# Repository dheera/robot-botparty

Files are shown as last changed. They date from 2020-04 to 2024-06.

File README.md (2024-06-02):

# BotParty

A mini telepresence robot. At about $130 total for all parts (including the pictured used Pixel 1 phone), the goal of this robot is to be as inexpensive as possible for a complete telepresence solution.

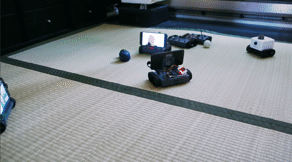
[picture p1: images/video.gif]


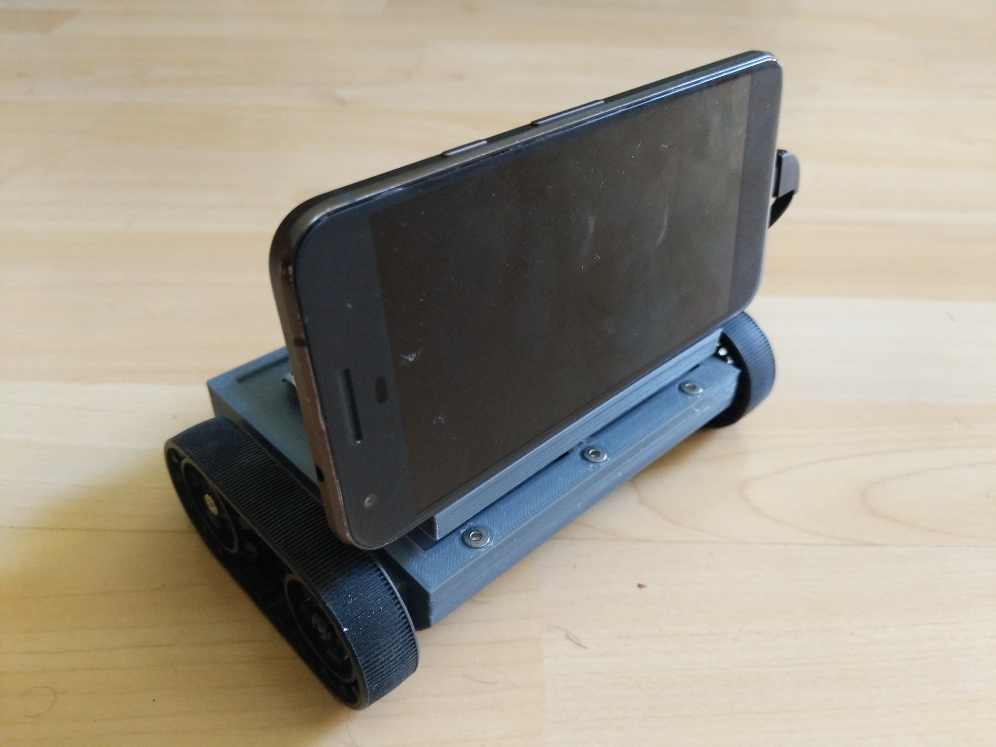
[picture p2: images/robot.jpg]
robot


Completed robot.

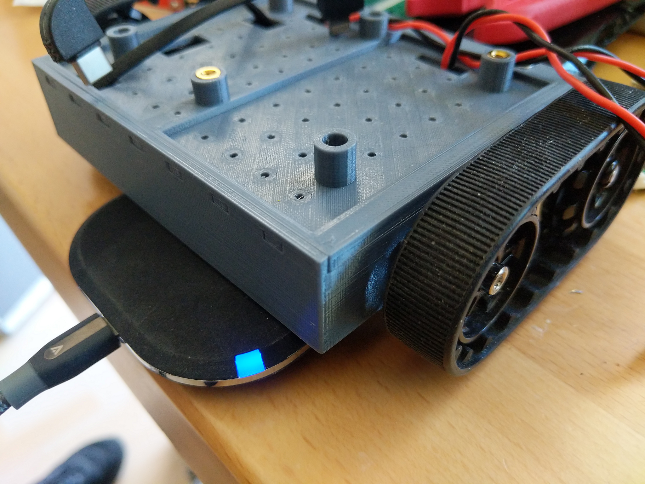
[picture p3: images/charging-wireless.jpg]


If you buy a 5V2A Qi charging sticker, you can charge the robot wirelessly just by driving on top of a wireless charger. Simple and no docking alignment fuss!

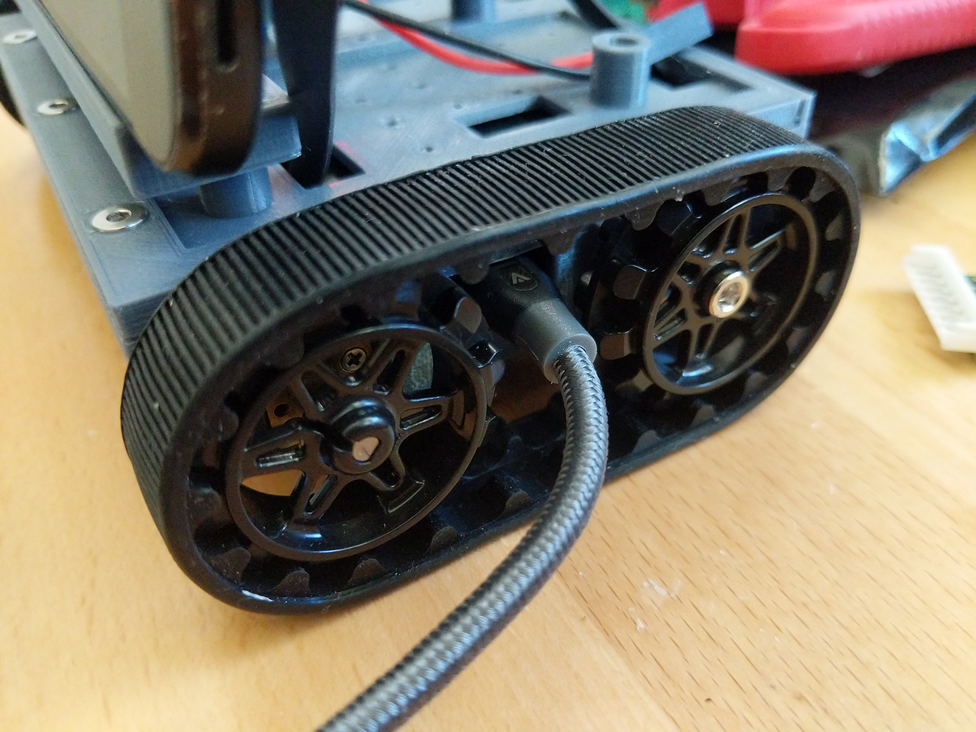
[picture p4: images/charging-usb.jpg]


You can use Anker Powerline micro-USB cables to charge the robot without taking it apart. *Not all micro-USB cables* will clear the outer edge of the sprocket.

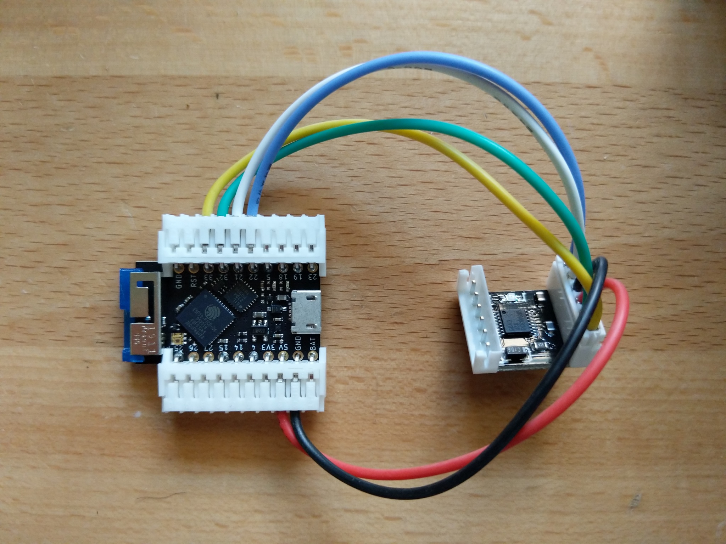
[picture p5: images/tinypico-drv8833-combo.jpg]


The motors are driven by a DRV8833 and a TinyPICO ESP32 microcontroller. The phone talks to the ESP32 over BLE. The ESP32 is super feature packed and also has Wi-Fi, capacitive touch sensing, I2C, SPI, UART, ADC, DAC, and lots of other features so you can build off this design and add whatever sensors and actuators you please. Build a security robot, a robot that roams around sensing VOC gas levels, and more!

## Assembly

### 3D printed parts

See .stl files in design/. I recommend printing in PETG. PLA sucks.

### Mechanical parts

* [M3 short heat-set inserts](https://www.mcmaster.com/94180a331), M3, OD=5.6mm, L=3.8mm -- [Possible alternative](https://www.ebay.com/sch/i.html?_from=R40&_trksid=m570.l1313&_nkw=initeq+m3+long&_sacat=0)
* [M3 long heat-set inserts](https://www.mcmaster.com/94180a333), M3, OD=5.6mm, L=6.4mm -- [Possible alternative](https://www.ebay.com/sch/i.html?_from=R40&_trksid=m570.l1313&_nkw=initeq+m3+short&_sacat=0)
* [Pololu 22T track set](https://www.pololu.com/product/3030)
* [M3 L=5mm countersunk screws](https://www.mcmaster.com/92125a125)
* [M3 L=5mm socket head screws](https://www.mcmaster.com/91292A110)

### Electronics
* [Used Google Pixel 1](https://www.ebay.com/sch/i.html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) -- You can get them used or "refurbished" for under $65. The charging cord on the portable charger below just barely fits so if you buy any bigger phone than the Pixel 1, you may need an extension on the charging cable. I do **not** recommend using an iPhone as Apple is consistently behind the times in terms of in-browser WebRTC support and doesn't even have bluetooth support from the browser. If you use an iPhone you will have to write an iOS native app from scratch.
* 2 x [Micro metal gearmotors](https://www.pololu.com/category/60/micro-metal-gearmotors) -- If you buy from Pololu, HPCB or HP 75:1 is proboblay the best for this use case but you can go up or down to 30:1 to 150:1 depending on your needs. Get single shaft if you don't plan on even putting encoders in, get dual-shaft if you think you might want encoders later. Get MP instead of HP/HPCB if you want a cheaper motor. Or search eBay/AliExpress for MUCH cheaper alternatives although many suppliers don't provide specs on current and stall torque making it hard to choose. There are also sometimes people on eBay reselling authentic used Pololu motors at cheaper prices.
* Portable charger: [YPLANG 9000mAh](https://www.amazon.com/Powerbank-9000mAh-Portable-Charger-External/dp/B07JMTSPC3) or [BeeFix 9000mAh](https://www.amazon.com/Portable-Charger-9000mAh-External-Battery/dp/B07SNV2B42/) or [Elephant Story 9000mAh](http://www.elephantstory.net/product/ds01/) -- They are the same charger under 2 different brand names). Make sure you get the version with 1 USB-C out + 1 lightning+microUSB combination out, and not their older version with 1 microUSB + 1 lightning. The chassis and 3D printed parts are designed to match this charger, which allows charging+discharging at the same time, and has two charging ports, one of which can be used for a Qi charger sticker.
* [2A Qi fast charging receiver USB-C](https://www.aliexpress.com/item/4000239832349.html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,searchweb201602_,searchweb201603_) if you want wireless charging where the robot can just drive up onto a charger (optional)
* 1 x DRV8833 carrier [No-name cheap 5 for $8 carrier](https://www.amazon.com/KOOBOOK-DRV8833-Module-Bridge-Controller/dp/B07S4FVY9M/) or [Pololu 1 for $4.95 DRV8833 carrier](https://www.pololu.com/product/2130) or any other DRV8833 carrier
* [TinyPICO](https://www.adafruit.com/product/4335) or other ESP32 board of your choice
* [24 AWG wire](https://www.amazon.com/gp/product/B07G2BWBX8/)
* [1x2 Dupont connector housing](https://www.pololu.com/product/1901) and [crimps](https://www.pololu.com/product/1930) or just get a [kit like this](https://www.amazon.com/gp/product/B078RRPRQZ/). [This crimper](https://www.amazon.com/Crimping-0-08-1-0-18-28AWG-Ratcheting-Connector/dp/B01N1RFZZ4/) has worked well for me for Dupont crimps.
* [JST-EH](https://www.digikey.com/catalog/en/partgroup/eh-series/) connectors for ESP32 board and ESP-DRV8833 connection (or use whatever you prefer). [This crimper](https://www.amazon.com/Engineers-Precision-Crimping-Pliers-Pa-09/dp/B002AVVO7K/) has worked well for me for JST-EH.

## Code

**esp32/** contains firmware for a TinyPICO. (a) Follow TinyPICO's instructions to enable the Arduino IDE (b) install the analogWrite library for ESP32 and then (c) compile it with Arduino. You can then visit the [ESP32 web terminal](https://dheera.github.io/esp32terminal/) to test connectivity. Steps to test:

- Use desktop Chrome on a laptop that has Bluetooth, or Chrome on Android also works. Chrome on iOS will not work.
- Go to chrome://flags/#enable-experimental-web-platform-features and enable.
- Go to the ESP32 web terminal and Connect to "tethys-255" which should be your newly flashed TinyPICO.
- If you connected successfully, you will see "Z" being output every second. That is a heartbeat from the firmware.
- Type "G 0 255 0 255" to drive the motors, and you can try other values as well. They are just PWM values for 2 H-bridges. The motors will stop after 1 second; this is expected as the ESP32 firmware imposes a 1 second heartbeat on incoming commands.
- Type "S 4" to set the robot number to 4 or whatever number you want <=255. This is a persistent setting. After a power cycle (unplug and replug the TinyPICO) the device will show up as "tethys-4". This allows you to prevent from connecting the wrong robot phone to the wrong robot ESP32.

**server/** contains server code. Run with node and proxy node through nginx for https (see nginx.conf and sites-available/default). Hacky, to be improved.

You MUST go to chrome://flags/#enable-experimental-web-platform-features on the robot and enable it! This is required for Chrome to be able to talk to BLE devices from a webpage. Only the robot needs this, not your participants.

https://yourserver/robot/#room on the robot with Chrome. You need to set a robot id and a passcode. Then every time you load the page on the robot you need to press the bluetooth button and select the "tethys-###" device. Unfortunately this is a limitation of the web bluetooth API and it cannot auto-connect without a user gesture.

https://yourserver/join/#room is for participants. Chrome on Linux/MacOS/Windows should all work. Issues have been reported on Safari and iOS and I need to get a hold of some Apple hardware to debug these.

WebRTC data channels [don't seem to renegotiate](https://stackoverflow.com/questions/61179293/renegotiating-sdp-withaudiovideodata-webrtc) so I use socket.io for driving and WebRTC for audio/video. Clunky but WebRTC documentation is lacking and all the examples suck at illustrating proper SDP renegotiation.

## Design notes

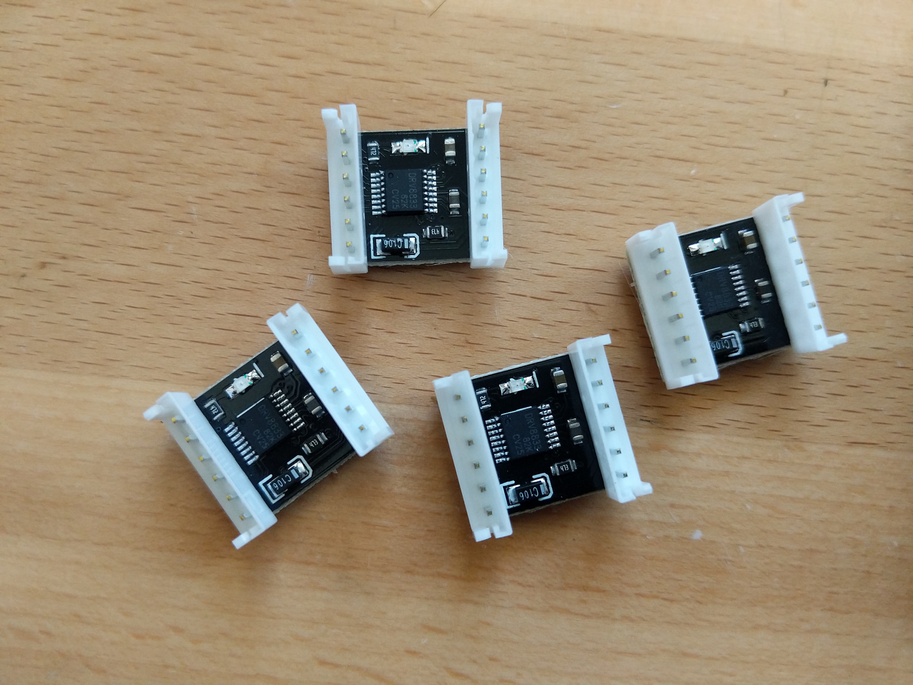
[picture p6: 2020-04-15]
images/drv8833-cheap-0.jpg

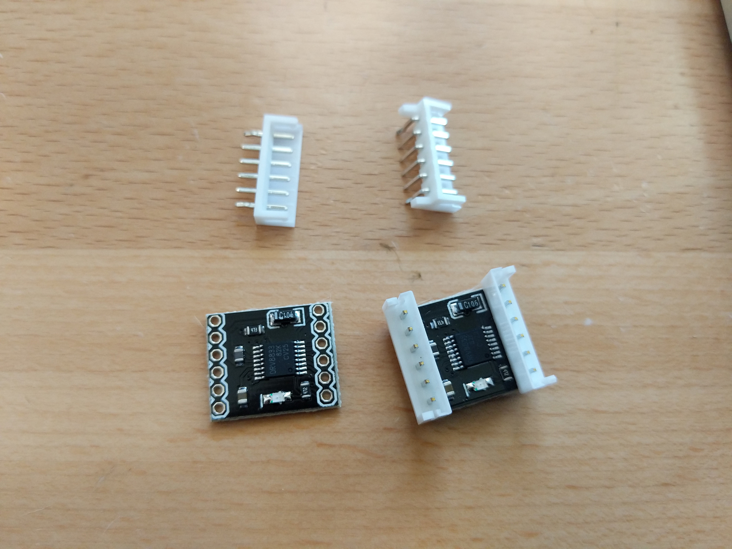
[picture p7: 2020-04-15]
images/drv8833-cheap-1.jpg

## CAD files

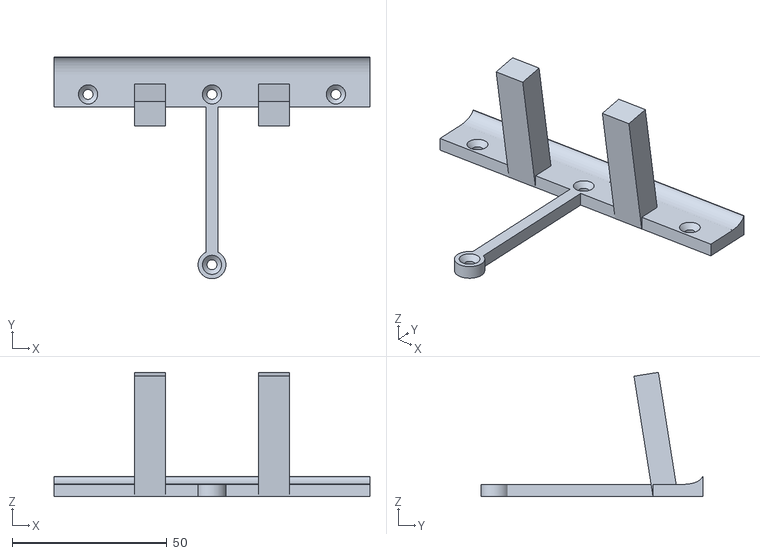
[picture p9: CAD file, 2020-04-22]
design/phone-mount.stl
102.0 x 71.5 x 40.1

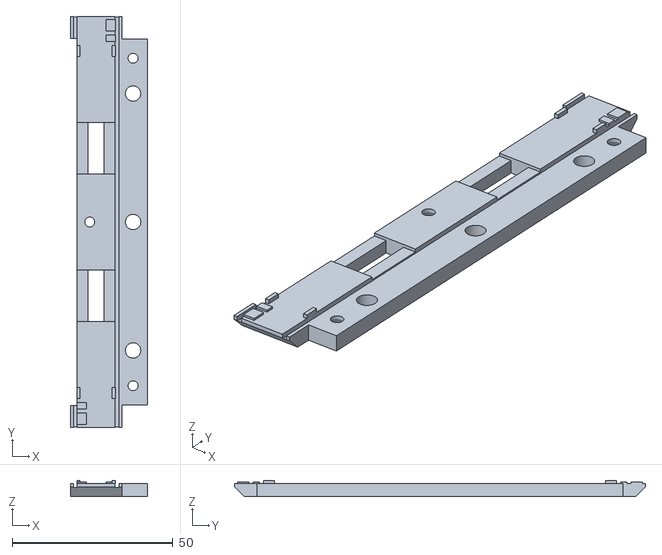
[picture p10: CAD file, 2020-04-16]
design/motor-cover.stl
24.0 x 128.0 x 5.00

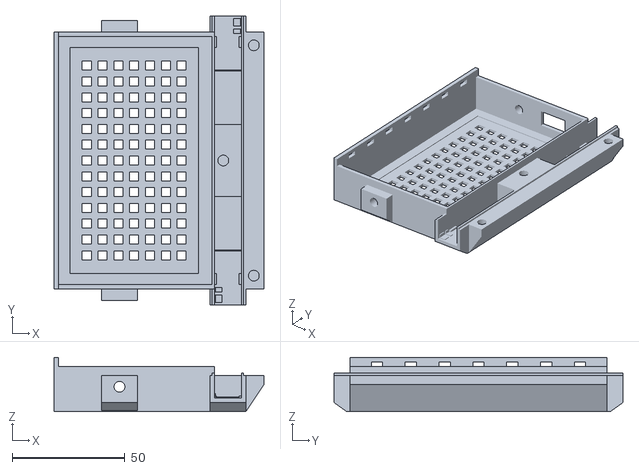
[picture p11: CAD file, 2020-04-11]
design/lower-chassis2.stl
93.0 x 128.0 x 24.0

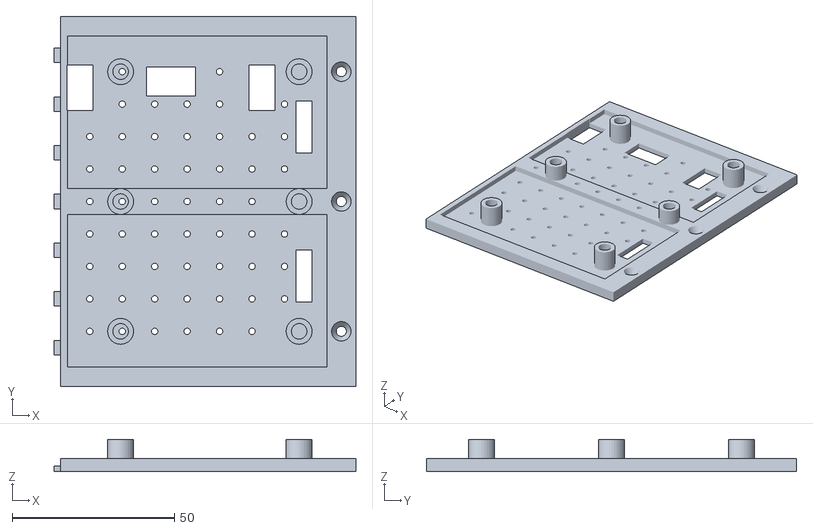
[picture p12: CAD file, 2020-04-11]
design/electronics-deck2.stl
93.0 x 114.0 x 10.0

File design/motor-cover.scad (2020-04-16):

batt_l = 68;
batt_w = 110;
batt_h = 18;

w_stretch = 2;
w_off = batt_l/2 - 16;

pi_l = 65;
pi_w = 56;
pi_hole_space_l = 58;
pi_hole_space_w = 49;

wheel_dist_l = 48;
m3_insert_d = 4.8;

t = 2;

    top_space = 4;
    h=12;
    
rotate([180,0,0]) {

difference() {
    union() {
        cube_center([16,batt_w+7+7 + 2*t,1]);
        cube_center([16,batt_w + 4 + 4 + 2*t,top_space]);

        translate([16/2+8/2,0,0])
        cube_center([8,batt_w+2*t,top_space]);

        translate([0,-batt_w/2-t-4,1])
        rotate([0,0,90])
        scale([3,16,3])
        triangle();

        translate([0,batt_w/2+t+4,1])
        rotate([0,0,90])
        scale([-3,16,3])
        triangle();

    }

translate([-7,0,0,])
cube_center([2,batt_w+2*t+0.2,10]);

translate([-6.5,0,0])
cube_center([1.2,150,1.2]);

translate([6.5,0,0])
cube_center([1.2,150,1.2]);

translate([11.5,-batt_w/2+4,0]) {
translate([0,0,1])
cylinder(d1=3.1,d2=6.1,h=3.001,$fn=32);
translate([0,0,0])
cylinder(d1=3.1,d2=3.1,h=3,$fn=32);
}

translate([11.5,batt_w/2-4,0]) {
translate([0,0,1])
cylinder(d1=3.1,d2=6.1,h=3.001,$fn=32);
translate([0,0,0])
cylinder(d1=3.1,d2=3.1,h=3,$fn=32);
}

translate([-2,0,0]) {
translate([0,0,1])
cylinder(d1=3.1,d2=6.1,h=3.001,$fn=32);
translate([0,0,0])
cylinder(d1=3.1,d2=3.1,h=3,$fn=32);
}

translate([11.5,-batt_w/2+15,0])
cylinder(d=m3_insert_d,h=5,$fn=32);
translate([11.5,0,0])
cylinder(d=m3_insert_d,h=5,$fn=32);
translate([11.5,batt_w/2-15,0])
cylinder(d=m3_insert_d,h=5,$fn=32);

translate([0,-24.5+3.5+2-4,0])
cube_center([12,16,0.75]);
translate([0,-24.5+3.5+2-4,0])
cube_center([5,16,4]);

translate([0,24.5-3.5-2+4,0])
cube_center([12,16,0.75]);
translate([0,24.5-3.5-2+4,0])
cube_center([5,16,4]);

}


translate([-12/2+3/2,batt_w/2+7+t-3.5/2-1,-.5])
cube_center([3,3.5,0.5]);

translate([-12/2+3/2,batt_w/2+7+t-2/2-5.75,-.5])
cube_center([3,2,0.5]);

translate([12/2-1/2,batt_w/2+7+t-3.5/2-9,-1])
cube_center([1,3.5,1]);

translate([-12/2+1/2,batt_w/2+7+t-3.5/2-9,-1])
cube_center([1,3.5,1]);

rotate([0,0,180]) {
translate([-12/2+3/2,batt_w/2+7+t-3.5/2-1,-.5])
cube_center([3,3.5,0.5]);

translate([-12/2+3/2,batt_w/2+7+t-2/2-5.75,-.5])
cube_center([3,2,0.5]);
    
translate([12/2-1/2,batt_w/2+7+t-3.5/2-9,-1])
cube_center([1,3.5,1]);

translate([-12/2+1/2,batt_w/2+7+t-3.5/2-9,-1])
cube_center([1,3.5,1]);
}

}

module cube_center(dims) {
    translate([-dims[0]/2, -dims[1]/2, 0])
    cube(dims);
}
 
module triangle() {
rotate([0,-90,90])
linear_extrude(height = 1, center = true, convexity = 10, twist = 0)
polygon(points=[[0,0],[0,1],[1,0]]);
}

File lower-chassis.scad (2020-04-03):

batt_l = 68;
batt_w = 108;
batt_h = 19;


w_off = batt_l/2 - 16;

pi_l = 65;
pi_w = 56;
pi_hole_space_l = 58;
pi_hole_space_w = 49;

wheel_dist_l = 48;
m3_insert_d = 4.8;

t = 2;

    //h=9.5+t*2+2;
    
    top_space = 4;
    h=12;


translate([0,0,35])
rotate([0,0,90])
cube_center([105,65,17]);



    translate([batt_l/2+7+1.5*t,0,0])
    cube_center([16,batt_w+2*t,6]);

difference() {
    cube_center([batt_l+2*t,batt_w+2*t,batt_h + t]);
    translate([0,0,t])
    cube_center([batt_l,batt_w,batt_h * 2]);
    
        translate([-wheel_dist_l/2+w_off,0,(h+t)/2+batt_h+t-h-top_space])
        rotate([90,0,0])
        cylinder(d=m3_insert_d, h=100, center=true, $fn=32);
}

wheelbars();

module cube_center(dims) {
    translate([-dims[0]/2, -dims[1]/2, 0])
    cube(dims);
}



module wheelbars() {
    
    //h=15.5;
    
    translate([0,0,batt_h+t - h - top_space])
    difference() {
        union() {
            
            translate([0,batt_w/2+t+3.5,0])
            translate([6+t/2,0,0])
            cube_center([batt_l + 2*t + 16 + t, 7, h]);
            translate([0,-(batt_w/2+t+3.5),0])
            translate([6+t/2,0,0])
            cube_center([batt_l + 2*t + 16 + t, 7, h]);
            
            translate([batt_l/2 + 6 + t*1.5 ,0,0])
            cube_center([16+t,batt_w + 2*t, h]);
        
            translate([-wheel_dist_l/2+w_off,batt_w/2+t-2,-5])
            triangle2();
            translate([wheel_dist_l/2+w_off,batt_w/2+t,-5])
            triangle2();
        translate([-wheel_dist_l/2+w_off,-(batt_w/2+t)+2,-5])
            scale([1,-1,1])
        triangle2();
        translate([wheel_dist_l/2+w_off,-(batt_w/2+t),-5])
            scale([1,-1,1])
            triangle2();    
                    
        }
    
        translate([14.5,batt_w/2 + 7, 0])
        cube_center([32, 10, h]);
        
        translate([14.5,-(batt_w/2 + 7), 0])
        cube_center([32, 10, h]);
        
        translate([-32.5,batt_w/2 + 7, 0])
        cube_center([30, 10, h]);
        
        translate([-32.5,-(batt_w/2 + 7), 0])
        cube_center([30, 10, h]);
        
        
        translate([-32.5,-(batt_w/2 + 7+ 5), 0])
        cube_center([80, 10, h]);
        
        translate([-32.5,(batt_w/2 + 7+ 5), 0])
        cube_center([80, 10, h]);
        
        translate([-wheel_dist_l/2+w_off,0,(h+t)/2])
        rotate([90,0,0])
        cylinder(d=m3_insert_d, h=100, center=true, $fn=32);
        
        
    translate([wheel_dist_l/2+w_off-3,-0,h-6])
        cylinder(d=m3_insert_d,h=100,$fn=32);
        
        // motor mount cutouts
        for(sign=[-1:2:1])
        translate([wheel_dist_l/2+w_off,sign*(batt_w/2 + t +7 - 38/2),t])
        rotate([0,0,sign*90+90])
        motor_mount_cutout();
        
    }
    
}

module motor_mount_cutout() {
        difference() {
            union() {
                cube_center([12,38.001,9.5+5]);
                translate([0,-38/2+24+5/2,0])
                cube_center([14,5,9.5+5]);
            }
            translate([-4,-38/2+1+3.5/2,0])
            cube_center([3,3.5,0.5]);
            translate([-5.75,-38/2+1+3.5/2,0])
            cube_center([0.5,3.5,2]);
            
            translate([-4,-38/2+5.75+2/2,0])
            cube_center([3,2,0.5]);
            translate([-5.75,-38/2+5.75+2/2,0])
            cube_center([0.5,2,2]);
            
            translate([0,-38/2+24+0.3/2,0])
            cube_center([14,0.3,0.5]);
            
            translate([-12/2+1/2,-38/2+9+5/2,0])
            cube_center([1,5,1]);
            translate([12/2-1/2,-38/2+9+5/2,0])
            cube_center([1,5,1]);
        }
}

translate([+batt_l/2+2*t+14,0,0])
{
    difference() {
        scale([-1,1,1]) triangle();
        translate([3,30,batt_h+t-top_space - 6.5])
        cylinder(d=m3_insert_d,h=100,$fn=32);
        translate([3,-30,batt_h+t-top_space - 6.5])
        cylinder(d=m3_insert_d,h=100,$fn=32);
    }
}

module triangle() {
scale([1,1,1])
rotate([0,-90,90])
linear_extrude(height = batt_w+2*t, center = true, convexity = 10, twist = 0)
polygon(points=[[0,0],[12,8],[batt_h+t-top_space,8],[batt_h+t-top_space,0]]);
}

module triangle2() {
scale([1,1,1])
rotate([0,-90,0])
linear_extrude(height = 16, center = true, convexity = 10, twist = 0)
polygon(points=[[0,0],[5,7],[5,0]]);
}

for(q=[0:1:1])
translate([w_off +17.5+ q*13,0,batt_h + t - top_space])
difference() {
    cube_center([1,batt_w+2*7+2*t,1]);
    for(sign=[-1:2:1])
    translate([0,sign*(batt_w/2-17.5),0])
    cube_center([5,5,5]);
}

translate([-batt_l/2-t/2,0,batt_h+t]) {
    difference() {
        cube_center([2,batt_w+2*t,4]);
        cube_center([2,5,2]);
        translate([0,-15,0])
        cube_center([2,5,2]);
        translate([0,15,0])
        cube_center([2,5,2]);
        translate([0,-30,0])
        cube_center([2,5,2]);
        translate([0,30,0])
        cube_center([2,5,2]);
    }
}

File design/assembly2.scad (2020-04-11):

breakaway=0;

import("lower-chassis2.stl");

translate([41.5+breakaway,0,16+breakaway])
import("motor-cover.stl");

translate([0-2*breakaway,0,20.0+2*breakaway])
import("electronics-deck2.stl");

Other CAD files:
design/electronics-deck2.scad
design/lower-chassis2.scad
design/phone-mount.scad

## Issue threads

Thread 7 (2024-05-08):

How can I get the hardware kit.

zhangzhengde0225, 2024-05-08:
Hello, I'm enginner in China.

I want to by the hardware kit of the robot, How can I get that?

think you

dheera, 2024-07-24:
Hi,
You can 3D print all the parts and assemble it yourself, unfortunately I don't have a kit to sell.
Some minor changes may be needed if some of these parts are no longer available.

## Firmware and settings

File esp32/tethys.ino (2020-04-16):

#include <Arduino.h>

#include <TinyPICO.h>

#include <BLEDevice.h>
#include <BLEServer.h>
#include <BLEUtils.h>
#include <BLE2902.h>

#include <EEPROM.h>
#include <analogWrite.h>

#define EEPROM_SIZE 1

#define BAUDRATE 115200


#define SERVICE_UUID "6e400001-b5a3-f393-e0a9-e50e24dcca9e"
#define CHARACTERISTIC_UUID_RX "6E400002-B5A3-F393-E0A9-E50E24DCCA9E"
#define CHARACTERISTIC_UUID_TX "6E400003-B5A3-F393-E0A9-E50E24DCCA9E"

BLEServer *pServer;
BLEService *pService;
BLECharacteristic *pTxCharacteristic;
BLECharacteristic *pRxCharacteristic;

bool deviceConnected = false;
std::string rxValue = "";

void ble_send(std::string msg) {
  Serial.print("# sending: ");
  Serial.println(msg.c_str());
  pTxCharacteristic->setValue((byte*)msg.c_str(), msg.size());
  pTxCharacteristic->notify();
}

int pinMapping[4] = {22,21,32,33};

unsigned long last_command_time = 0;

void on_ble_receive(std::string msg) {
  // command format: 3 bytes:
  // ['P'] [channel] [value]
  // sets PWM of channel to value

  char str[256];
  strcpy(str, msg.c_str());
  const char* delim = " ";
  char* token;

  token = strtok(str, delim);

  if(strcmp(token,"G")==0) {
    token = strtok(NULL, delim);
    int channel = 0;
    while(token != NULL) {
      Serial.print("channel ");
      Serial.print(channel);
      Serial.print(" -> ");
      int value = atoi(token);
      Serial.println(value);
      analogWrite(pinMapping[channel], value);
      
      token = strtok(NULL, delim);
      channel++;
    }

    last_command_time = millis();
  } else if(strcmp(token, "S")==0) {
    token = strtok(NULL, delim);
    unsigned char robot_id = atoi(token);
    EEPROM.write(0, robot_id);
    EEPROM.commit();
    Serial.print("set robot id -> ");
    Serial.println((int)robot_id);
  }

}


class MyServerCallbacks : public BLEServerCallbacks
{
    void onConnect(BLEServer *pServer)
    {
        Serial.println("# connected");
        deviceConnected = true;
    }
    void onDisconnect(BLEServer *pServer)
    {
        Serial.println("# disonnected");
        deviceConnected = false;
    }
};

class MyCallbacks : public BLECharacteristicCallbacks
{
    void onWrite(BLECharacteristic *pCharacteristic)
    {
        Serial.print("# received: ");
        rxValue = pCharacteristic->getValue();
        Serial.println(rxValue.c_str());
        on_ble_receive(rxValue);
    }
};

void setup() {



    for(int channel=0;channel<4;channel++) {
      pinMode(pinMapping[channel], INPUT);
      digitalWrite(pinMapping[channel], LOW);
    }
    
    EEPROM.begin(EEPROM_SIZE);

    int bot_num = EEPROM.read(0);
    
    Serial.begin(BAUDRATE);

    char robot_name[256];
    sprintf(robot_name, "tethys-%d", bot_num);
    BLEDevice::init(robot_name);
    pServer = BLEDevice::createServer();
    pServer->setCallbacks(new MyServerCallbacks());

    pService = pServer->createService(SERVICE_UUID);

    // TX
    pTxCharacteristic = pService->createCharacteristic(
        CHARACTERISTIC_UUID_TX,
        BLECharacteristic::PROPERTY_NOTIFY
    );
    pTxCharacteristic->addDescriptor(new BLE2902());

    // RX
    pRxCharacteristic = pService->createCharacteristic(
        CHARACTERISTIC_UUID_RX,
        BLECharacteristic::PROPERTY_WRITE
    );
    pRxCharacteristic->setCallbacks(new MyCallbacks());

    pService->start();
    pServer->getAdvertising()->start();
    
    Serial.println("# waiting for client connection ...");

    
}

void loop() {
    static unsigned long millis_last = 0;
    static unsigned long reset_last = 0;

    if (millis() - last_command_time >= 1000) {
      if(millis() - reset_last >= 1000) {
        reset_last = millis();
        for(int channel=0;channel<4;channel++) {
          analogWrite(pinMapping[channel], 0);
        }
      }
    }

    if (millis() - millis_last >= 1000) {
        millis_last = millis();

        if (deviceConnected) {
            char msg[] = "Z\n";
            ble_send(msg);

            Serial.println(touchRead(4));
        }
    }
}

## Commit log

2020-04-07 design updates
    [assembly.scad, electronics-deck.scad, electronics-deck.stl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]
2020-04-11 new designs to make wheel distance correct 48mm
    [assembly2.scad, electronics-deck2.scad, electronics-deck2.stl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]
2020-04-12 esp32 firmware
2020-04-13 rm old design
    [assembly.scad, electronics-deck.scad, electronics-deck.stl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]
2020-04-16 flip motor cover for 3d printing
    [motor-cover.scad, motor-cover.stl]
2020-04-16 change pin mapping for motor control to not use gpio strapping pins which results in robot wildly running at startup
